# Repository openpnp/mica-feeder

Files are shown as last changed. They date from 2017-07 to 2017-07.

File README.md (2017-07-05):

# Mica Feeder by Pham Thang

This is a fully automatic DC motor based SMT tape feeder design by Pham Thang. It was
originally posted as a thread in the OpenPnP mailing list.

This repository is intended to serve as a permanent home for the feeder design and has
been created with Thang's permission.

For more details, see [the original thread](https://groups.google.com/d/msgid/openpnp/caf85d6c-853d-4bf1-ad3a-7fc51f31e7b0%40googlegroups.com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).

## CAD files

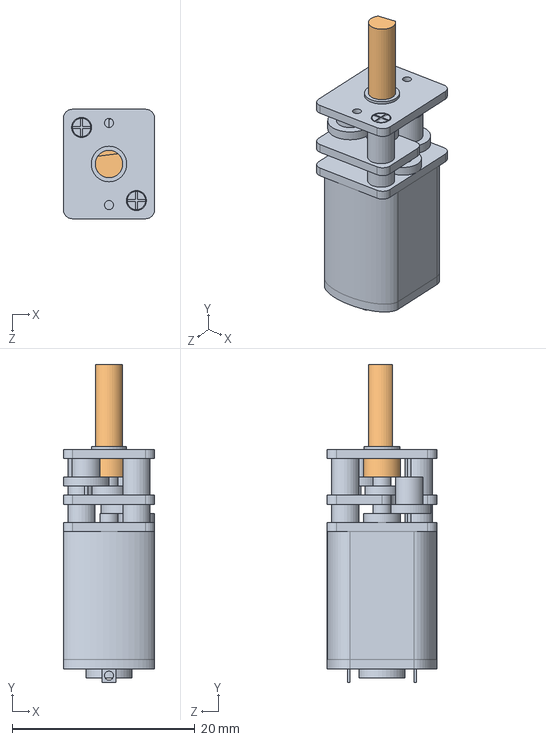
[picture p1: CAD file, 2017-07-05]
Solidworks/Micro DC reducer motor/Micro reducer DC motor.SLDASM
10.0 x 34.8 x 12.0 mm
Motor
Brazo

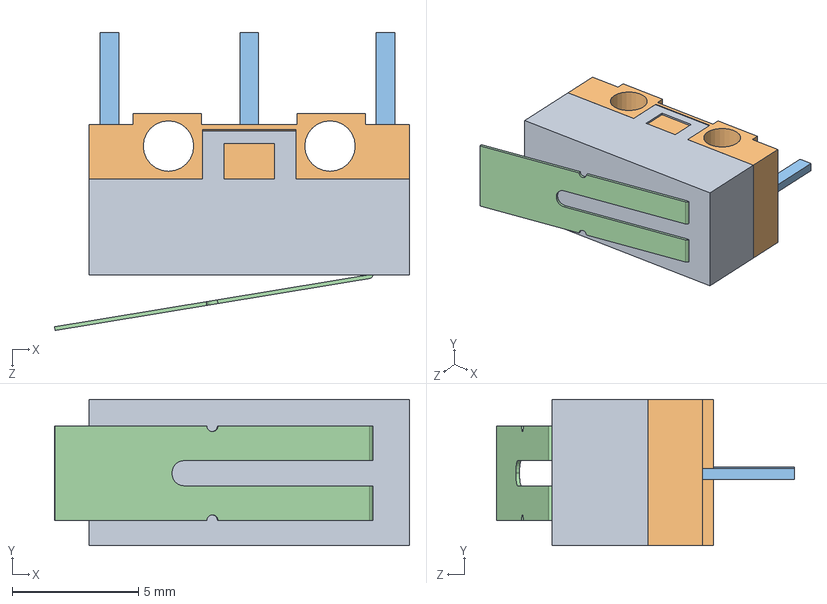
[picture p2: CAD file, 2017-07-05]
Solidworks/Micro switch button 1/botonera.SLDASM
14.1 x 5.80 x 11.8 mm
boton_01
boton_02
boton_03_patitas
boton_03_palancaClick

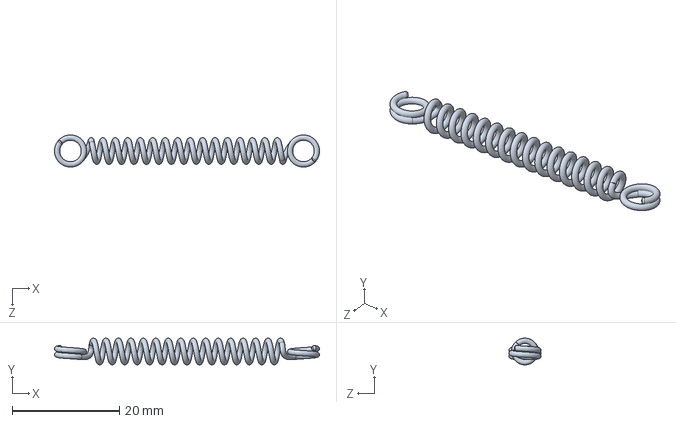
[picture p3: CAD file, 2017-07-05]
Solidworks/Spring motion analysis.SLDASM
49.5 x 5.00 x 5.99 mm

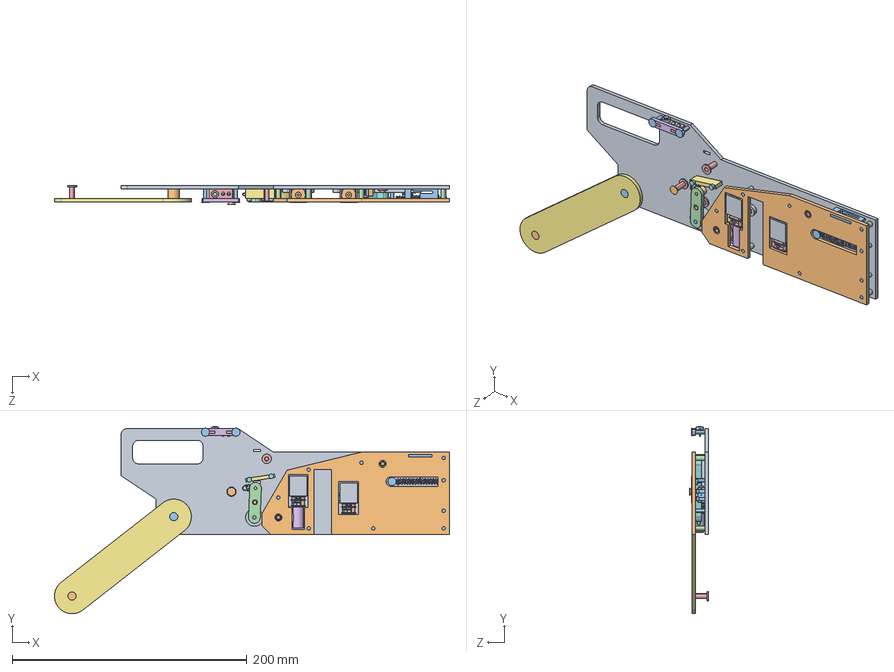
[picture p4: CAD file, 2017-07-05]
Mica feeder.STEP
336.7 x 159.7 x 16.1 mm
Feeder frame
Motor_Predeterminado x 2
Brazo_Predeterminado x 2
Bracket x 2
boton_01_Predeterminado x 2
boton_02_Predeterminado x 2
boton_03_patitas_Predeterminado x 2
boton_03_palancaClick_Predeterminado x 2
worm gear
gear
feed2
feed3
Cover
guide4
seesaw
pcba
PCBA cover
reel base
LED 3mm RED_Standard
LED 3mm Green_Standard
Micro button
wedge
M3 0.5 14mm screw x 13
Wedge1 x 7
female m3 screw x 6
Tension spring
gear1
M3 0.5 8mm screw x 9
M3 0.5 11mm screw
M2 6mm screw x 4
M2 10mm screw x 4
spring peeling
Tape guide
M2 13mm screw x 2

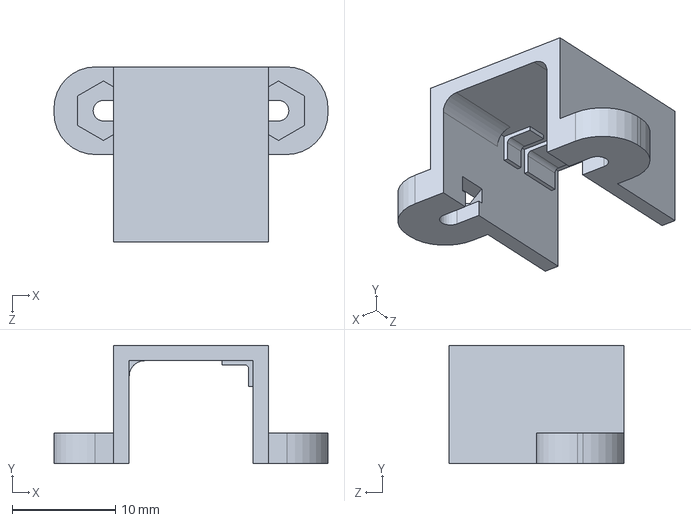
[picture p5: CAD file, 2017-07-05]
Solidworks/Micro DC reducer motor/Bracket.SLDPRT
26.6 x 11.5 x 17.0 mm

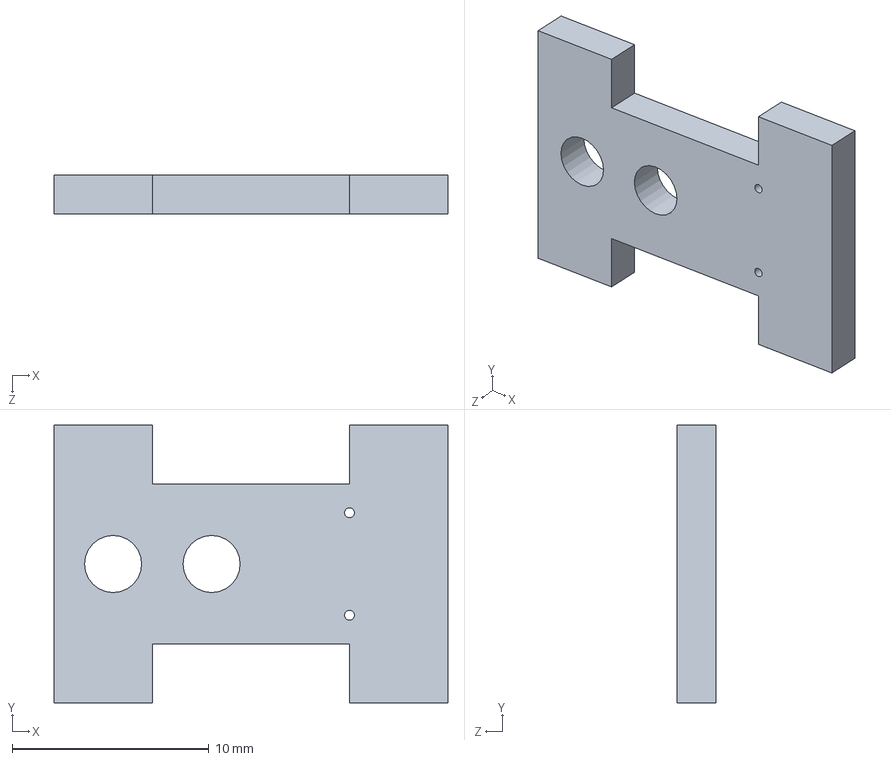
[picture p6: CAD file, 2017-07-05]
Solidworks/pcba.SLDPRT
20.0 x 14.1 x 2.00 mm

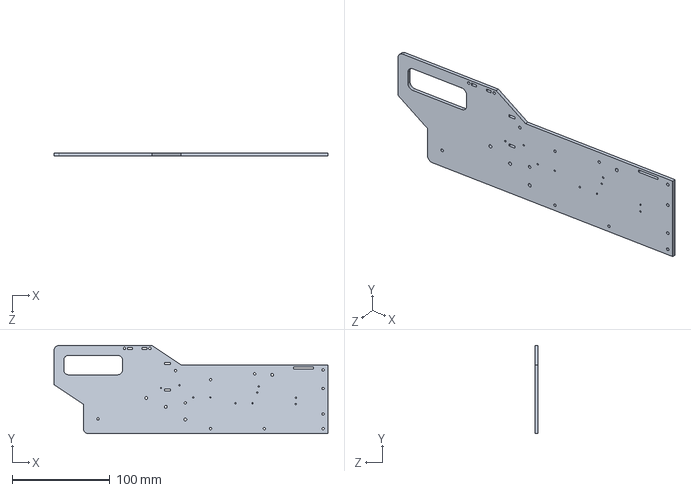
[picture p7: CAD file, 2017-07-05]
Solidworks/Feeder frame.SLDPRT
280.0 x 90.0 x 3.00 mm

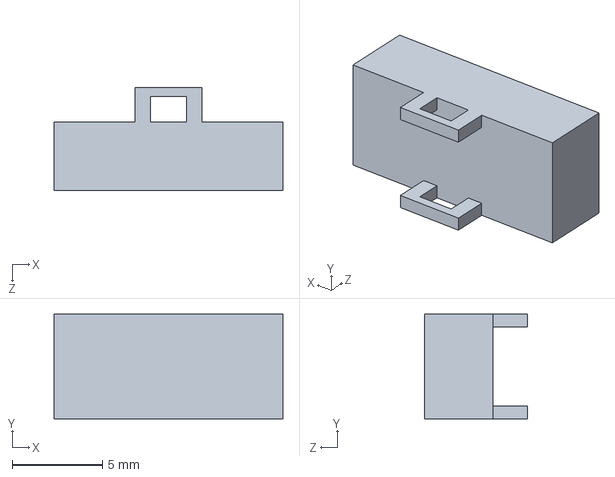
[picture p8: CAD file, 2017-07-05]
Solidworks/Micro switch button 1/boton_01.SLDPRT
12.7 x 5.80 x 5.70 mm

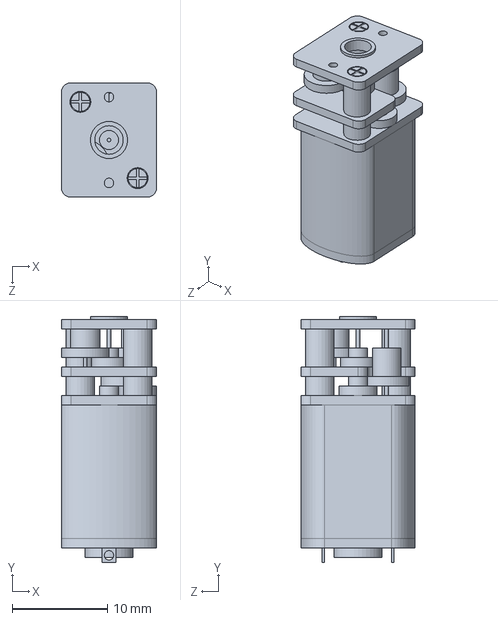
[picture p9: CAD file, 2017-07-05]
Solidworks/Micro DC reducer motor/Motor.SLDPRT
10.0 x 25.8 x 12.0 mm

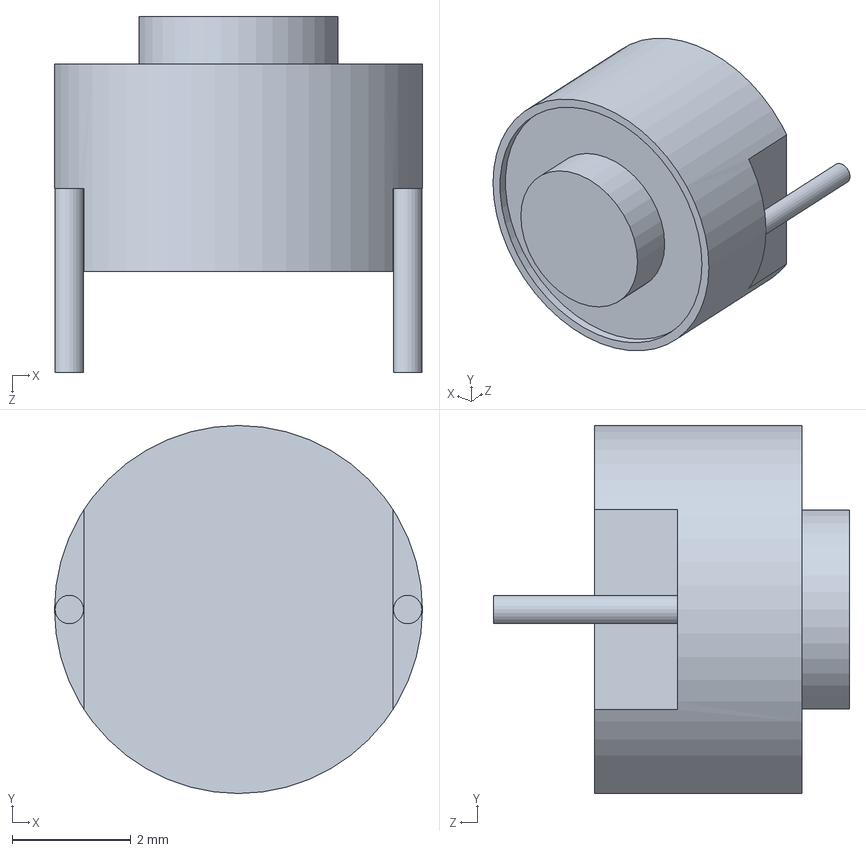
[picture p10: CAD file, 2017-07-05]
Solidworks/Micro button.SLDPRT
6.20 x 6.20 x 6.00 mm

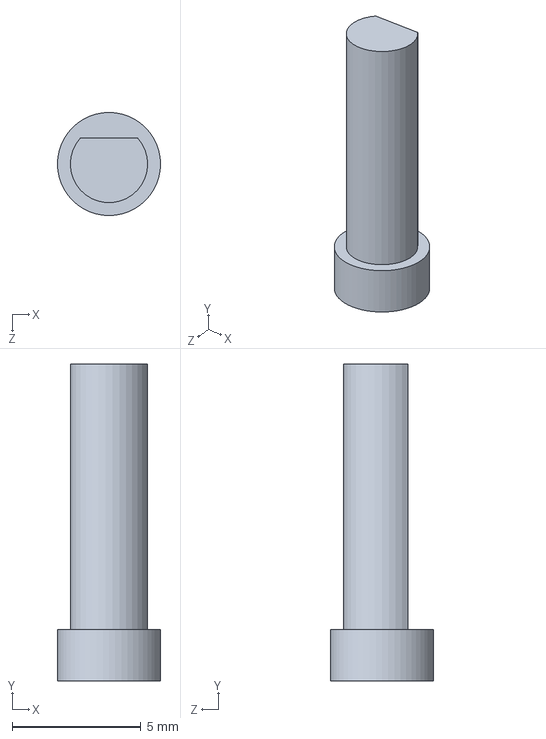
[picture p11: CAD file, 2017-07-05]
Solidworks/Micro DC reducer motor/Brazo.SLDPRT
4.00 x 12.3 x 4.00 mm

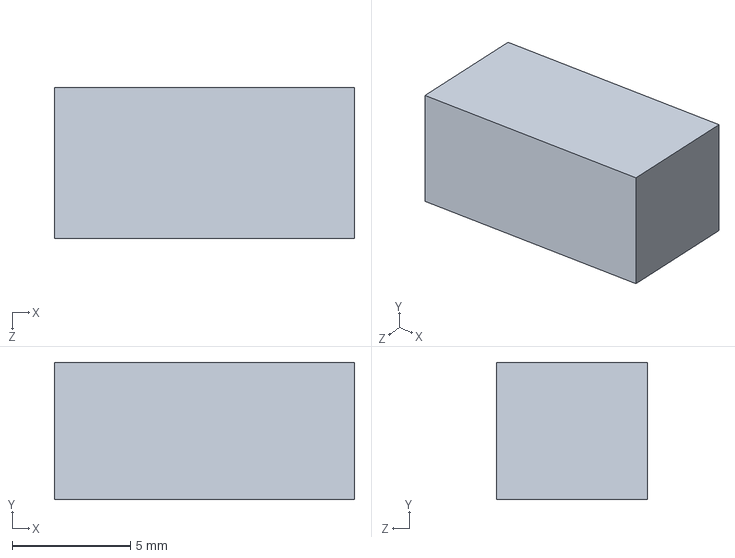
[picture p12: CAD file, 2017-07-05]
Solidworks/Micro switch button 1/boton_02.SLDPRT
12.7 x 5.80 x 6.40 mm

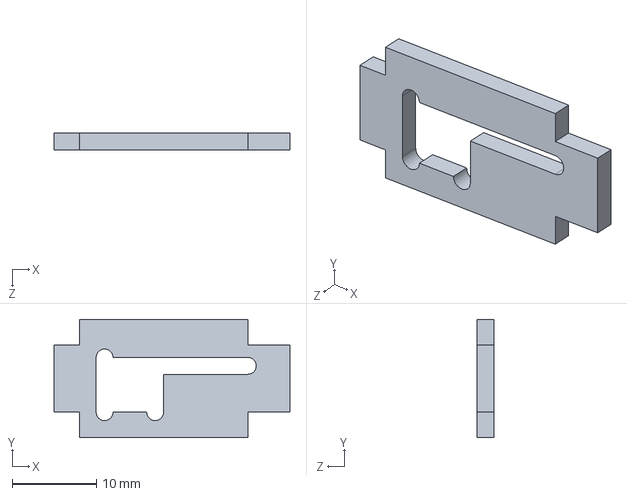
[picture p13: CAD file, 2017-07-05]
Solidworks/guide4.SLDPRT
28.0 x 14.0 x 2.00 mm

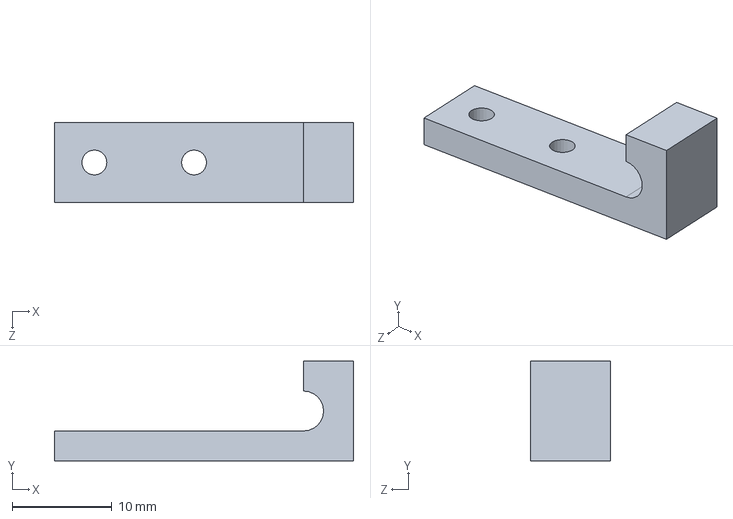
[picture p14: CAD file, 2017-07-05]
Solidworks/feeder base1.SLDPRT
30.0 x 10.0 x 8.00 mm

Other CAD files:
Solidworks/Micro switch button 1/boton_03_patitas.SLDPRT
Solidworks/Tension spring.sldprt
Solidworks/Micro switch button 1/boton_03_palancaClick.SLDPRT
Solidworks/Wedge1.SLDPRT
Solidworks/Cover.SLDDRW
Solidworks/Cover.SLDPRT
Solidworks/Feeder base.SLDPRT
Solidworks/LED 3mm Green.SLDPRT
Solidworks/LED 3mm RED.SLDPRT
Solidworks/M2 10mm screw.SLDPRT
Solidworks/M2 13mm screw.SLDPRT
Solidworks/M2 6mm screw.SLDPRT
Solidworks/M3 0.5 11mm screw.SLDPRT
Solidworks/M3 0.5 14mm screw.SLDPRT
Solidworks/M3 0.5 8mm screw.SLDPRT
Solidworks/Mica feeder.SLDASM
Solidworks/Mica feeder.SLDDRW
Solidworks/Micro Switch Button.SLDPRT
Solidworks/PCBA cover.SLDPRT
Solidworks/Tape guide.SLDPRT
Solidworks/electric wire holder.SLDPRT
Solidworks/feed2.SLDPRT
Solidworks/feed3.SLDPRT
Solidworks/feeder base2.SLDPRT
Solidworks/female m3 screw.SLDPRT
Solidworks/gear.SLDPRT
Solidworks/gear1.SLDPRT
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

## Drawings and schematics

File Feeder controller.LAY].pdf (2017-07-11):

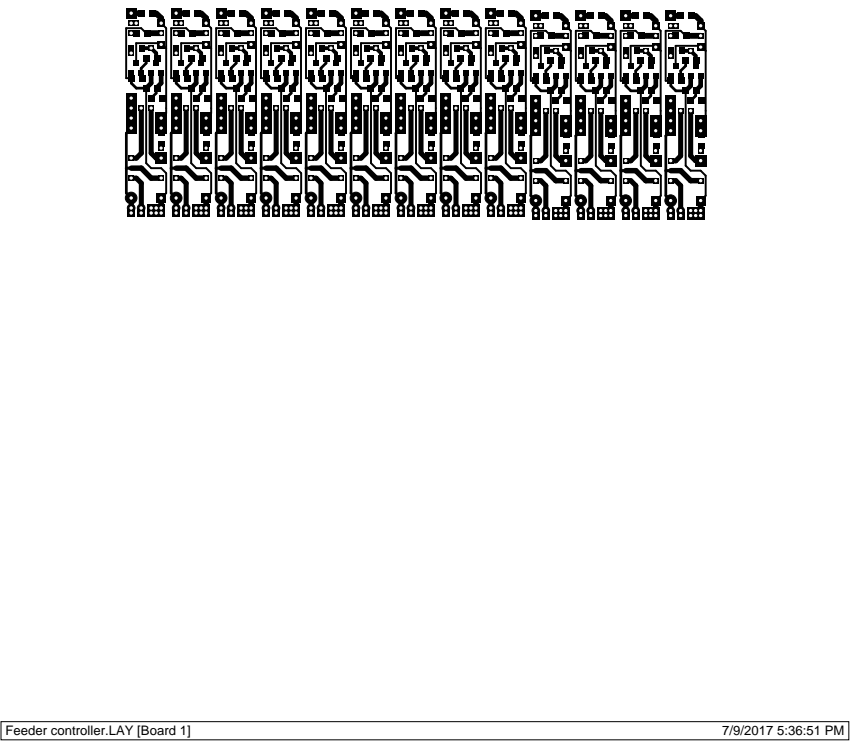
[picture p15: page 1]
Feeder controller.LAY [Board 1]

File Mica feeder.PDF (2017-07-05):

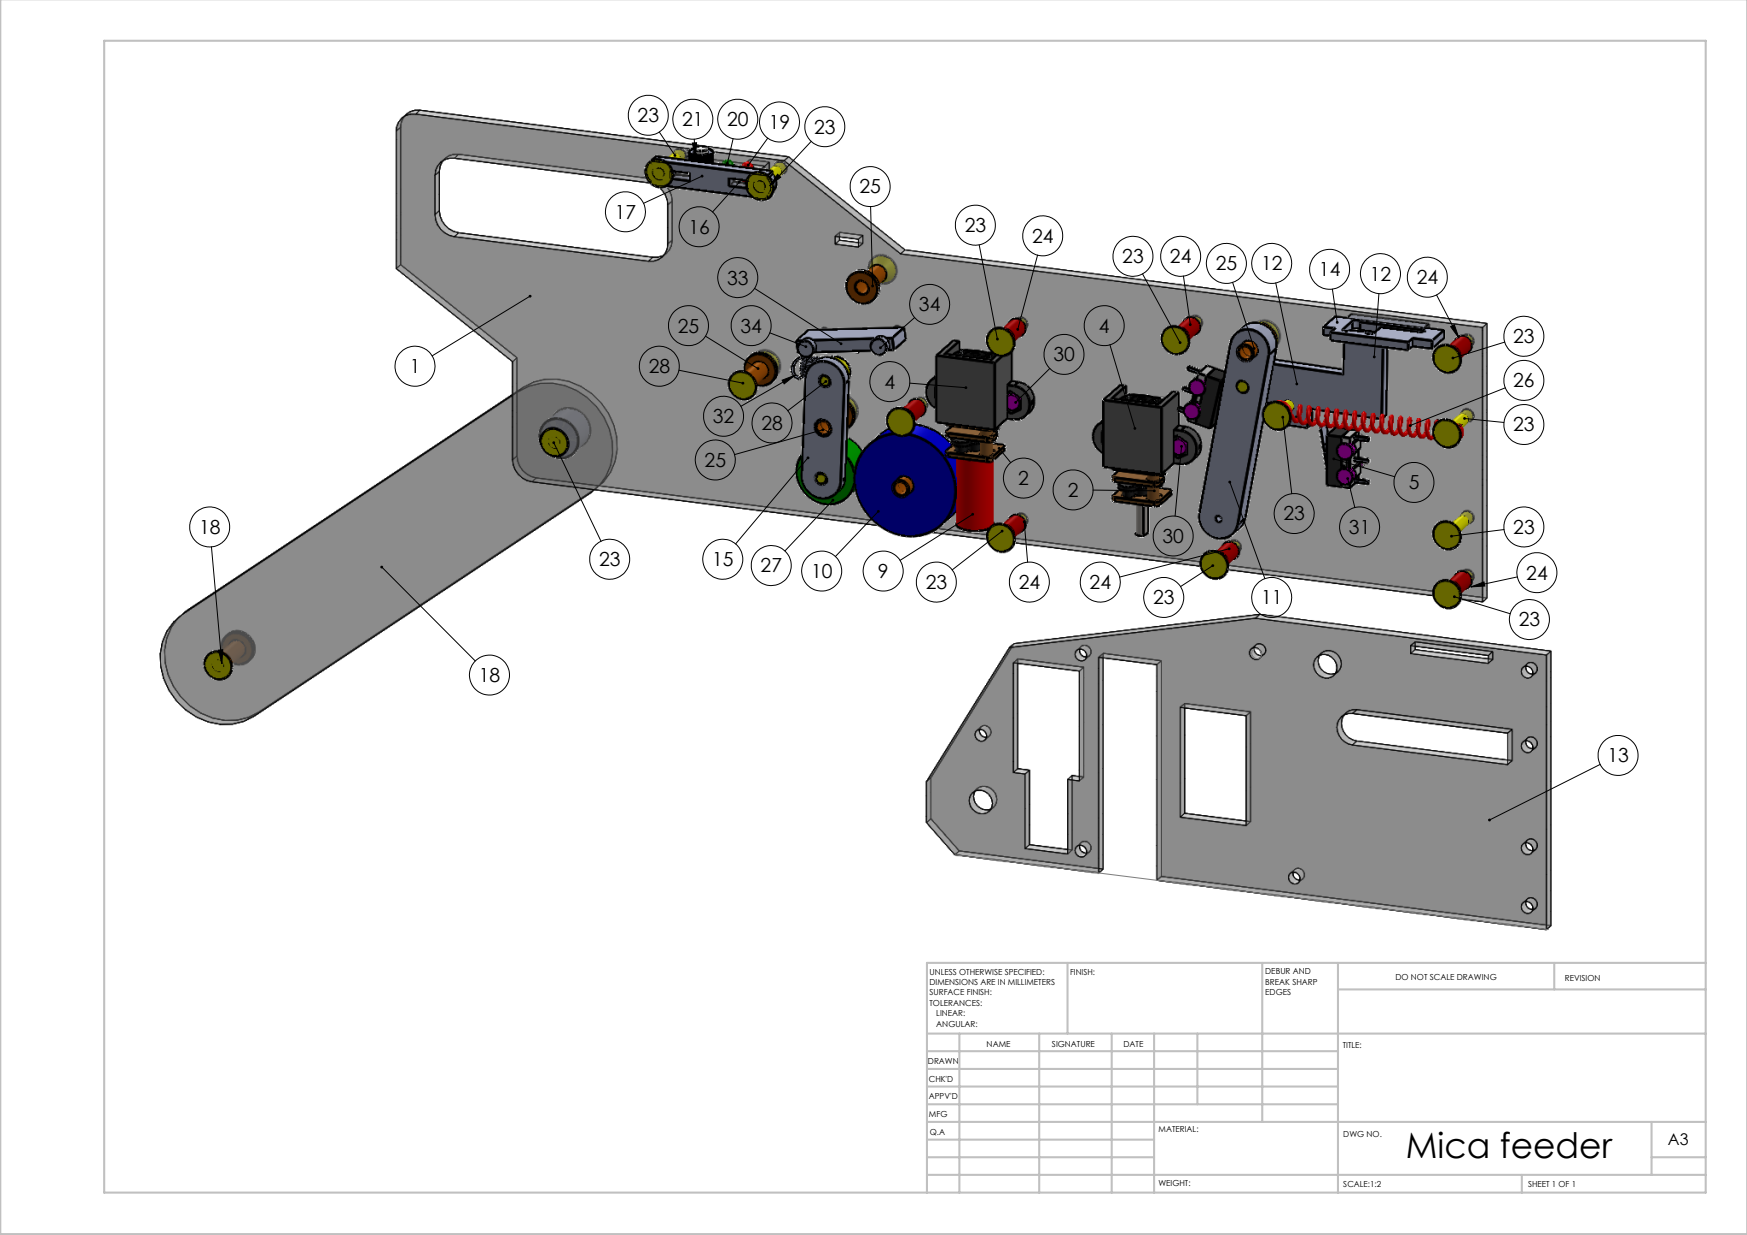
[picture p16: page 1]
SCALE:1:2; SHEET 1 OF 1; DO NOT SCALE DRAWING; REVISION; DEBUR AND BREAK SHARP; UNLESS OTHERWISE SPECIFIED:; FINISH:

DIMENSIONS ARE IN MILLIMETERS
SURFACE FINISH:
TOLERANCES:
LINEAR:
ANGULAR:

NAME | SIGNATURE | DATE | | | | TITLE:
Q.A | | | | MATERIAL: | Mica feeder WEIGHT: DWG NO. | A3

DRAWN
CHK'D
APPV'D
MFG

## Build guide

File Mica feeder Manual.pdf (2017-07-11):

Prepare By: Thang Pham

Copyright@2017-Thang pham

# Mica feeder

# Implementation and Maintenance Manual

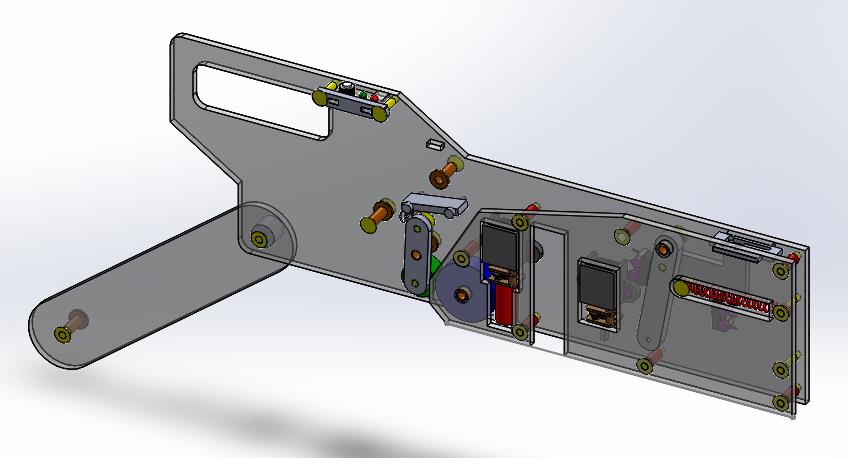
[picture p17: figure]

# TPA Tech, HCMC

# Automation Department

Version:1

Date：2017.7

Contents

1. Introduction
2. Feeder Key Compartments
3. Feeder Operation
4. Maintenance

### 1. Introduction

The Mica feeder was designed for Jason’s Open PnP machine with low cost and

easily for implementation and maintenance.

Feature

- Feeding speed 3600 CPH
- Peeling system by worm gear
- High accuracy and reliability
- Manual feeding mode

### 2. Feeder Key Compartments

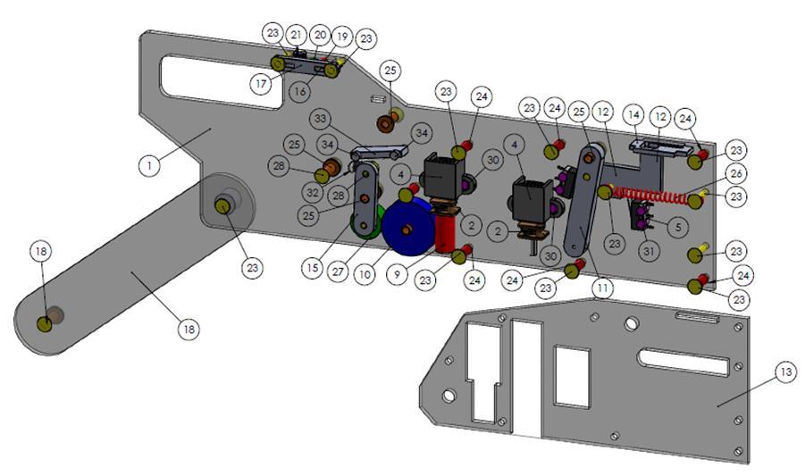
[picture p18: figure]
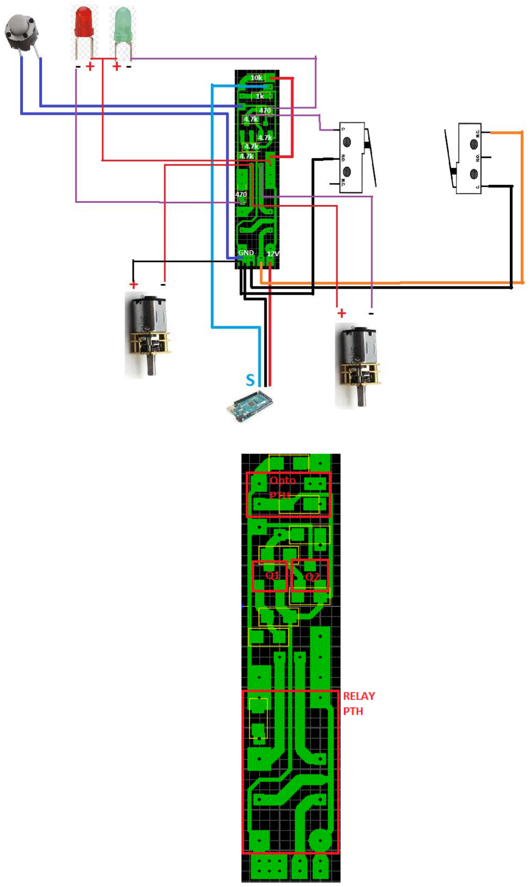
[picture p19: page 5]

Feeder mechanical BOM

Item | Part number | Description | Quantity | Actual picture
1 | 01 | Feeder main | 1
2 | 02 | Micro DC reducer motor (1:20) | 2
3 | 04 | Micro DC reducer motor bracket | 2
4 | 05 | Micro switch | 2
5 | 09 | Worm gear | 1
6 | 10 | Big gear | 1
7 | 11 | Feeding seesaw | 1
8 | 12 | Feeding | 1
9 | 13 | Feeder cover | 1

10 | 14 | Feeding plate | 1
11 | 15 | Peeling seesaw | 1
12 | 16 | Manual panel control | 1
13 | 17 | Manual panel control holder | 1
14 | 18 | Reel holder | 1
15 | 19 | LED 3mm Red color | 1
16 | 20 | LED 3mm Green color | 1
17 | 21 | Micro button | 1
18 | 23 | M3 0.5/14mm screw | 12
19 | 24 | Wedge1 | 7

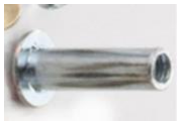
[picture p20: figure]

20 | 25 | M3 Female screwing | 4
21 | 26 | Feeding spring | 1
22 | 27 | Small gear | 1
23 | 28 | M3 0.5/6mm screw | 5
24 | 30 | M2 6mm screw | 4
25 | 31 | M2 10mm screw | 4
26 | 32 | Peeling spring | 1
27 | 33 | Reel base | 1
28 | 34 | M2 13mm screw | 2

Feeder PCBA BOM

Item | Description | Quantity | Actual picture
1 | Opto PC817 | 1
2 | Transistor C1815 | 2
3 | Relay 12v 8 pins HK19F-DC12V-SHG | 1
4 | Resistor 4.7k | 4
5 | Resistor 470 Ohm | 2
6 | Resistor 10k | 1
7 | Resistor 1k | 1

### 3. Feeder Operation

1. When we turn on the power supply (12v), transistor 1 closes, transistor 2 opens,

The feeding and peeling motor turn in a clockwise direction until the feeding lever

move to the front switch, cause break switch, both motors stops

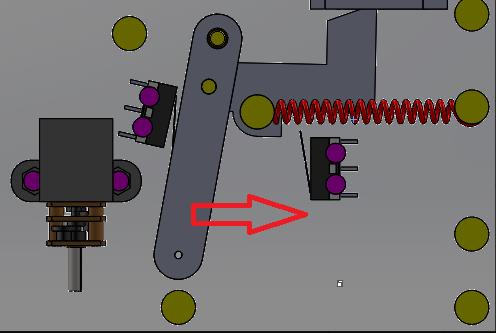
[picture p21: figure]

2. When the Feeder controller get 5v signal from sub-driver or 0V from feeding

manual mode, transistor 1 opens, transistor 2 closes, relay is triggered by

transistor 2 and converts the direction of feeding motor. The feeding lever comes

back ( the peeling motor no run)

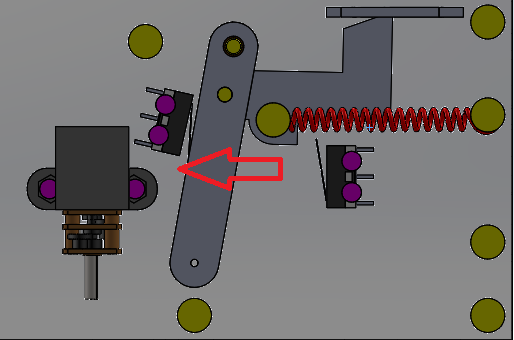
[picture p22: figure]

3. When the feeding lever comes back, impact to rear switch, transistor 1 closes,

transistor 2 opens. The feeding and peeling motor turn in a clockwise direction

until the feeding lever move to the front switch, cause break switch, both motors

stops, the reel moves 1 step.

### 4. Maintenance

Part | Method | Frequence
Motor | Check abnormal noise. If you find noise, please stop motor immediately and inform professional person. -Check temperature | Every monthly
Feeding and peeling lever | Check any abnormal noise during the movement | Every monthly
Micros witch | Check conductive of switch by VOM | Every monthly
Belt | Ware and tear | Every 3month
Feeding and peeling spring | Check the force of spring | Every 3month
Calibration | Check the accuracy | Every 3month
